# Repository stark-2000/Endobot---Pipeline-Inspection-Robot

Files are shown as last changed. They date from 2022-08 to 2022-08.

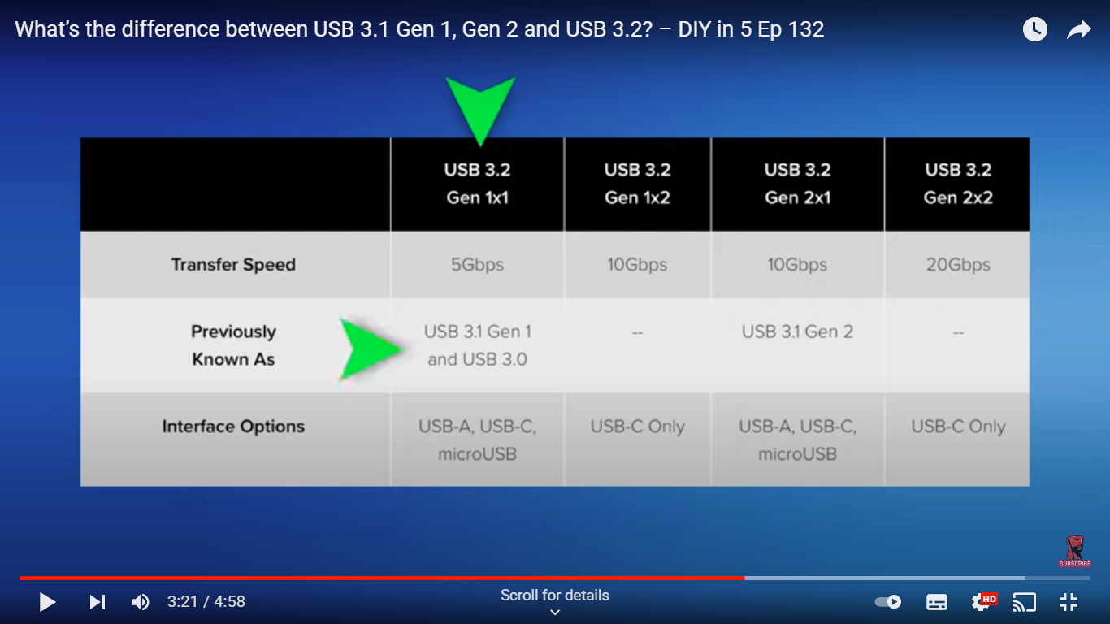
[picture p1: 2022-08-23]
Modules/Controller/USB - Case Study/USB Standards - Explained.png

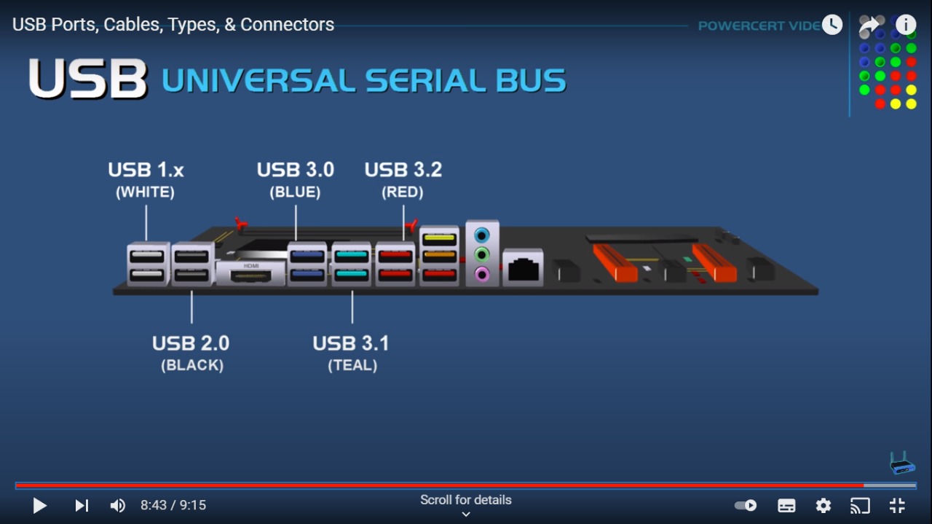
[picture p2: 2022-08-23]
Modules/Controller/USB - Case Study/USB Color Coding.jpeg

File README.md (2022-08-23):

Endobot 2.0, a tethered pipeline inspection robot which can detect leaks, corrosion and defects on pipelines as small as 4 inch up-to a depth of 300 meters and can withstand 5 bar underwater pressure.
It uses RS422 long distance data transfer protocol for camera feed & data transfer. The robot can be fully controlled from outside the pipeline using sophisticated controllers which enable 4 wheel drive and advanced transmission. 
Onboard IMU & Encoders enable accurate localisation & distance calculation of the robot. Realtime motor temp, indoor temp, pipeline leak sounds, current consumption, inclination calculation is all performed and displayed on a mini LCD screen.

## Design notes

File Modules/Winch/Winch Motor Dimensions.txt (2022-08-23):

Straight shaft motor: 
Case 1: 12cm max body length [done] (mounting outside spool perpendicular to spool axis)
Case 2: 30cm max body length [done] (mounting inside spool)
Case 3: Small length more dia (fat BLDC motor) [not available]

90 degree motor - 12cm max [2 vendors, one is WP AC motor, other chinese guy]

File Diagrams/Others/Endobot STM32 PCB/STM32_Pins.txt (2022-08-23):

TIM 1, 2, 3, 4, 5, 8, 9, 12 (Timers with PWM)

SPI4_SCK - White - PE12 - PWM - FT
SPI4_MISO - Blue - PE13 - PWM - FT
SPI4_MOSI - Green - PE14 - PWM - FT
SPI4_CS2 - Orange - PB12 - PWM - FT
GPIO_PB9 - Yellow - PB9 - PWM - FT
GPIO_PA10 - Brown - PA10 - PWM - FT

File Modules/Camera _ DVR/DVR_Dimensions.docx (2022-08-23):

DVR Layout

71mmm

51mm

Connectors

Record Stop

Joy Stick

Power ON/OFF

Logo

Distance Meter

LCD Screen

Screen Protection

- The DVR will have a battery backup of at least 1 Hour.

Depth - 50mm

110mm

190mm

Menu | Escape | Zoom in | Zoom Out

DVR Power ON/OFF Switch

Record Start

MIC (Push Button)

Screenshot

70mm

USB Storage Slot

Keyboard

90mm

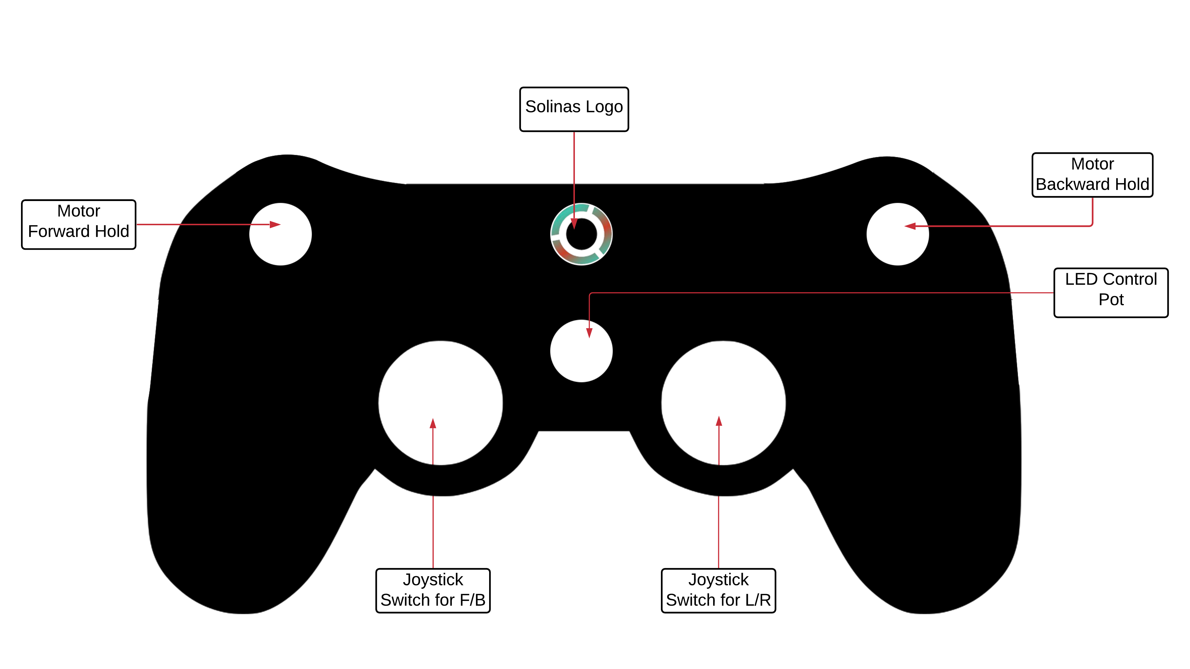
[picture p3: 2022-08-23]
Modules/Controller/Controller Design/Controller Design (labelled).png

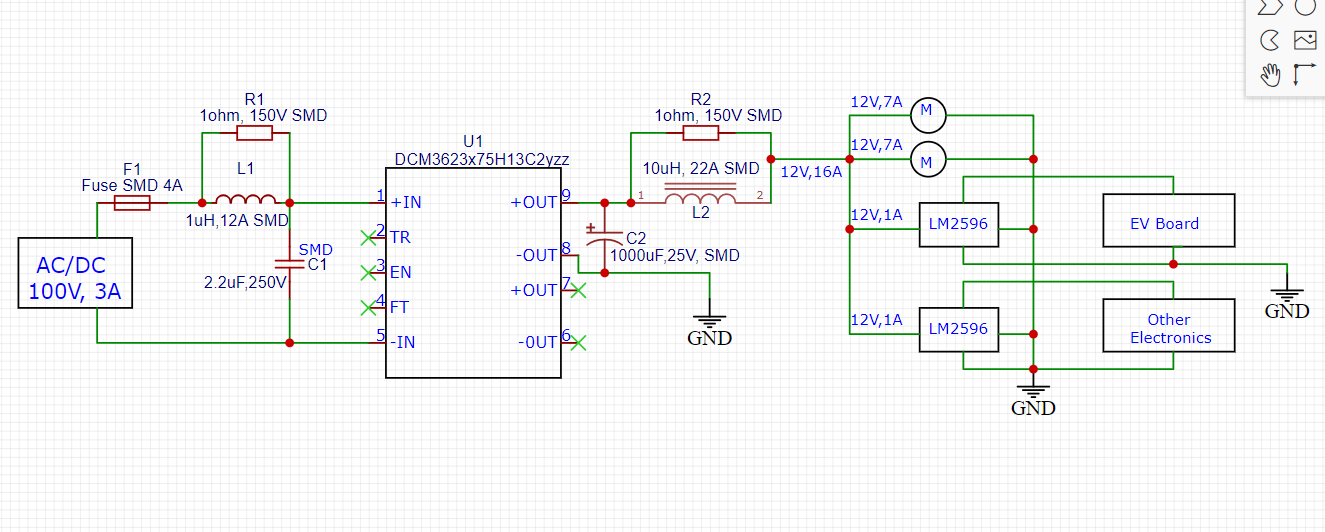
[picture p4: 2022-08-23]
Modules/Power Electronics/DC-DC Buck Converter/Vicor DCM/Buck Application Circuit.PNG

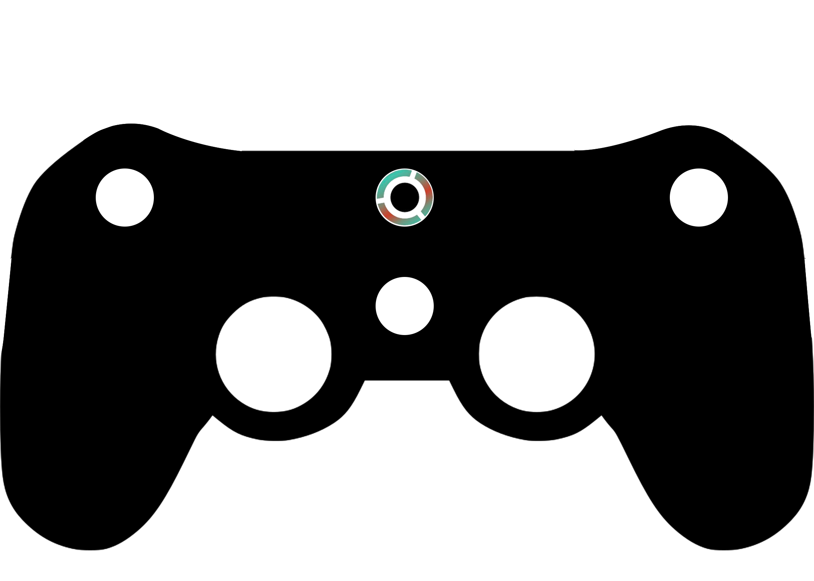
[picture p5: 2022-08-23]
Modules/Controller/Controller Design/Controller Design.png

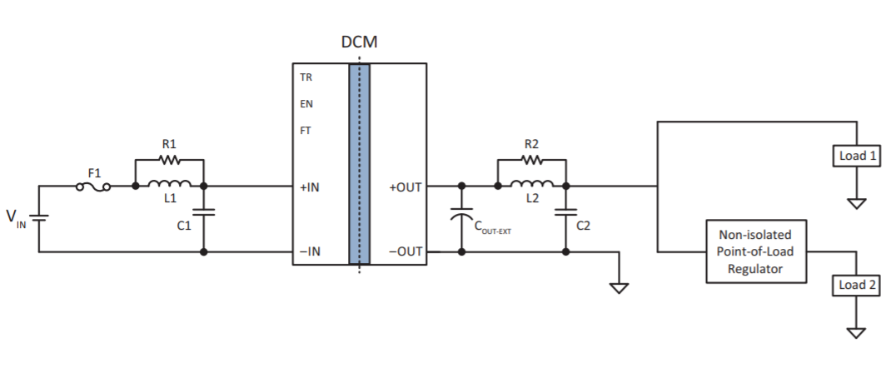
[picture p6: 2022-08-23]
Modules/Power Electronics/DC-DC Buck Converter/Vicor DCM/Buck 1 (DCM).PNG

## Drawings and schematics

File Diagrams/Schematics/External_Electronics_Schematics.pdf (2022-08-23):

## DC - DC Buck 24V

## SMPS 120V 5A DC

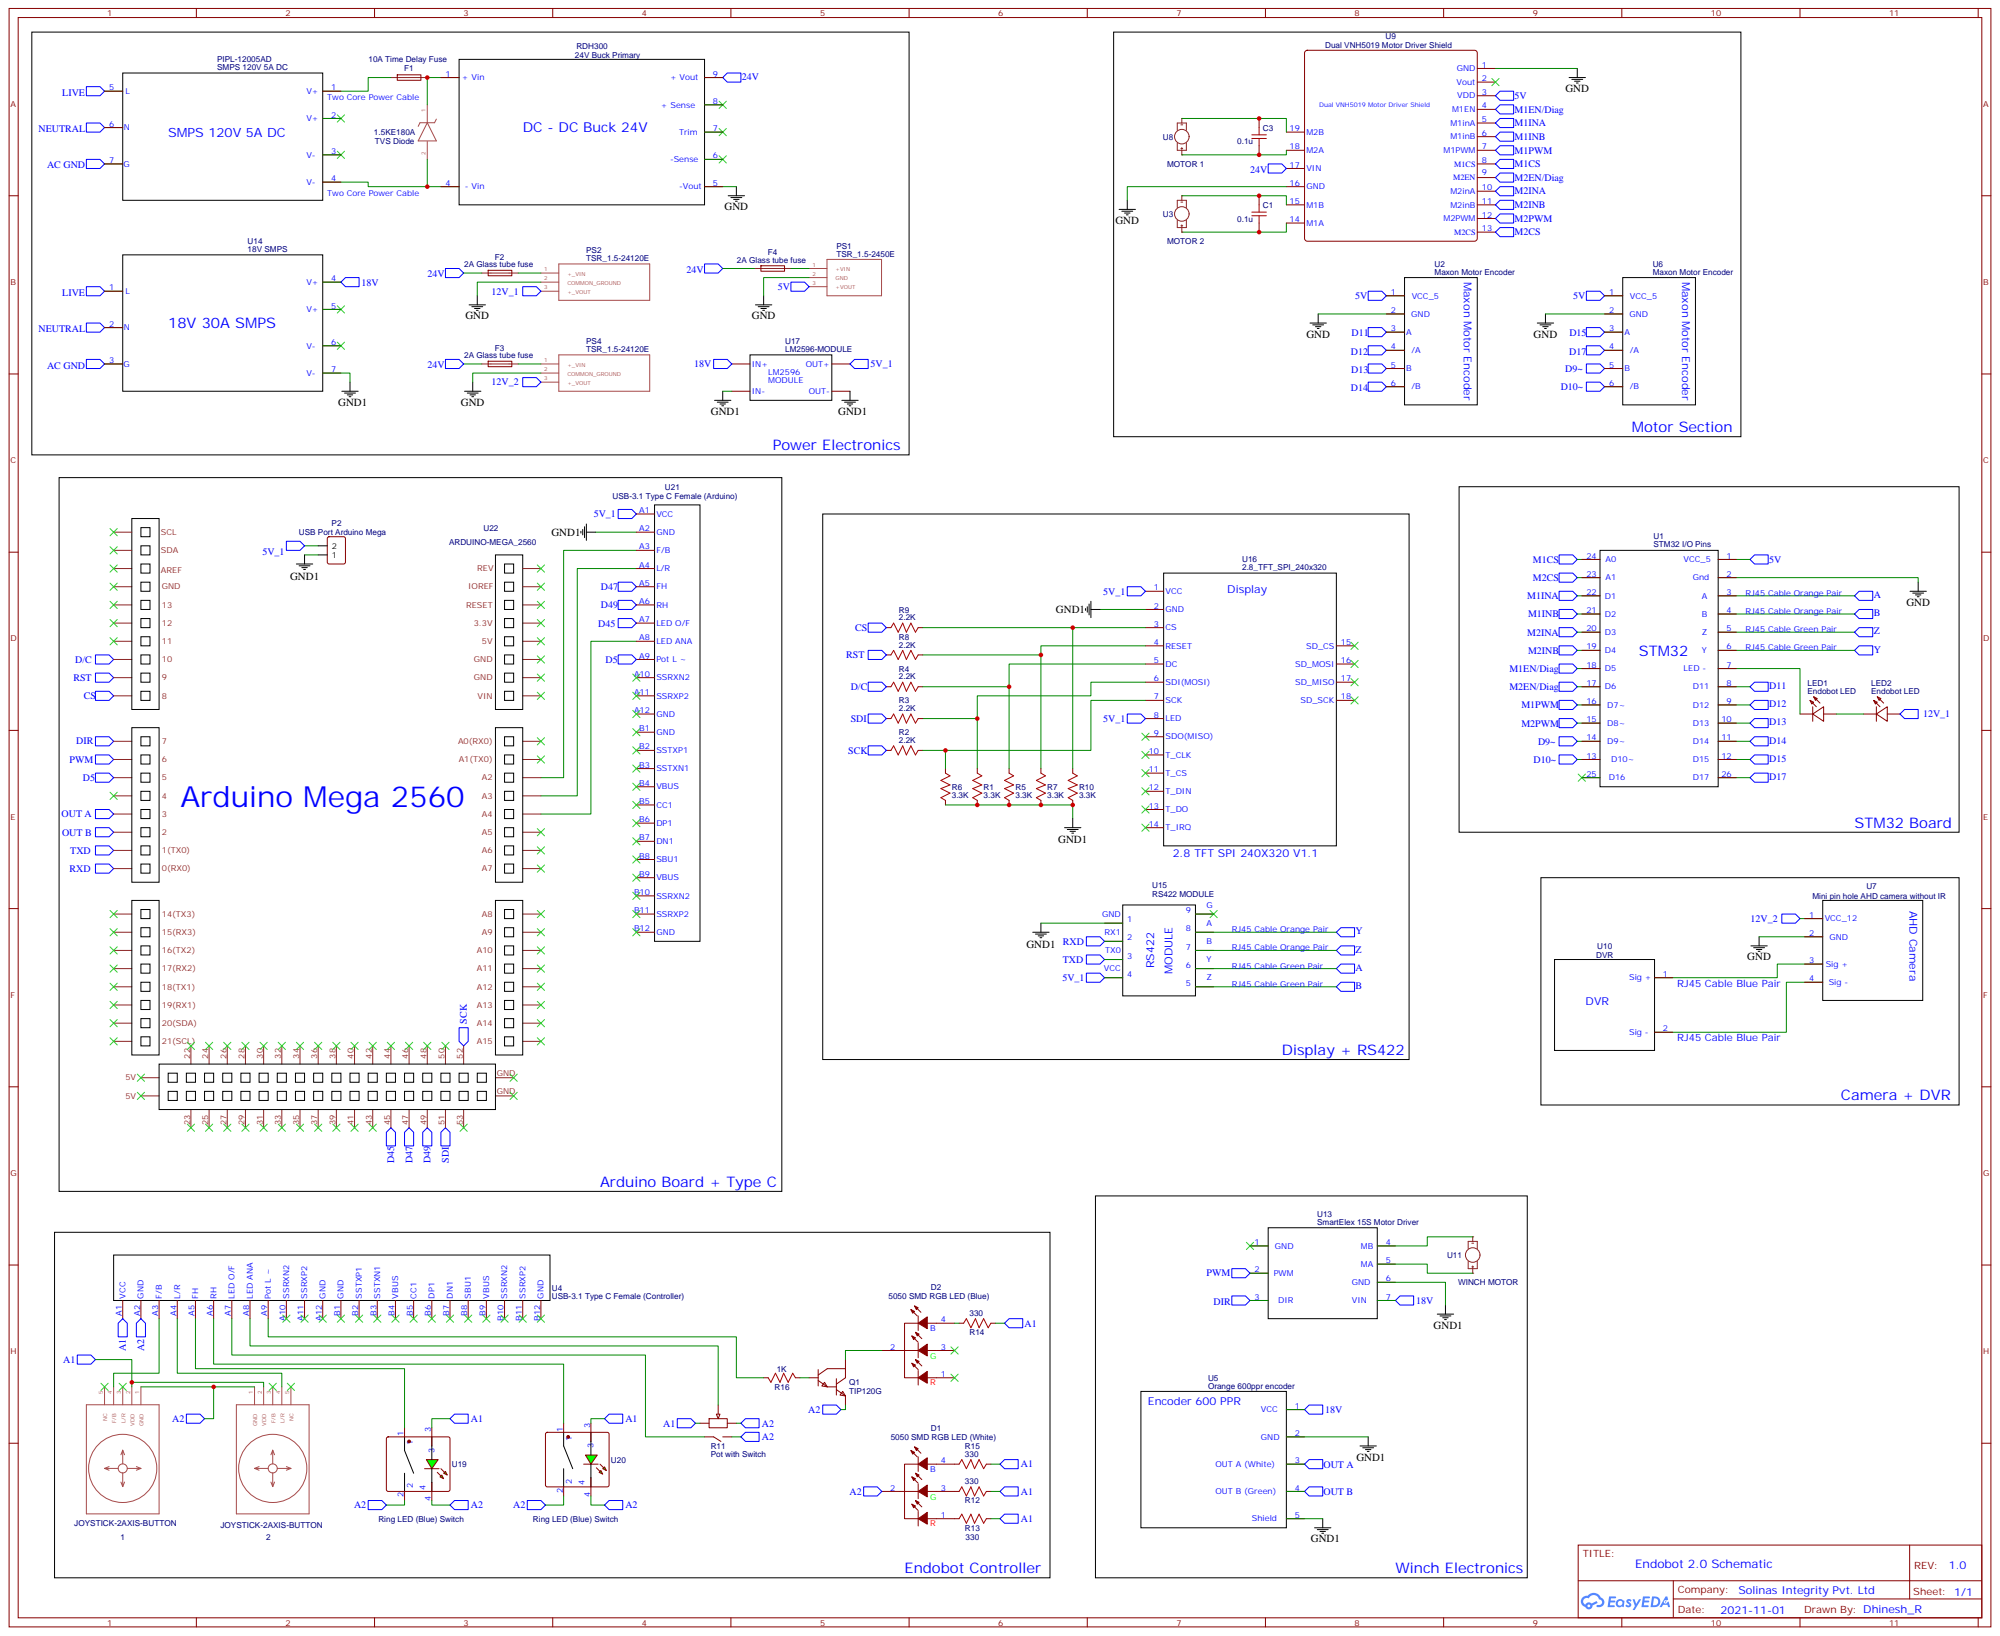
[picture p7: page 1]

Dual VNH5019 Motor Driver Shield

Two Core Power Cable

USB Port Arduino Mega

5050 SMD RGB LED (Blue)

Ring LED (Blue) Switch

Company: Solinas Integrity Pvt. Ltd

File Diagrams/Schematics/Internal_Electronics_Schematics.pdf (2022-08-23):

## Microcontroller Essentials

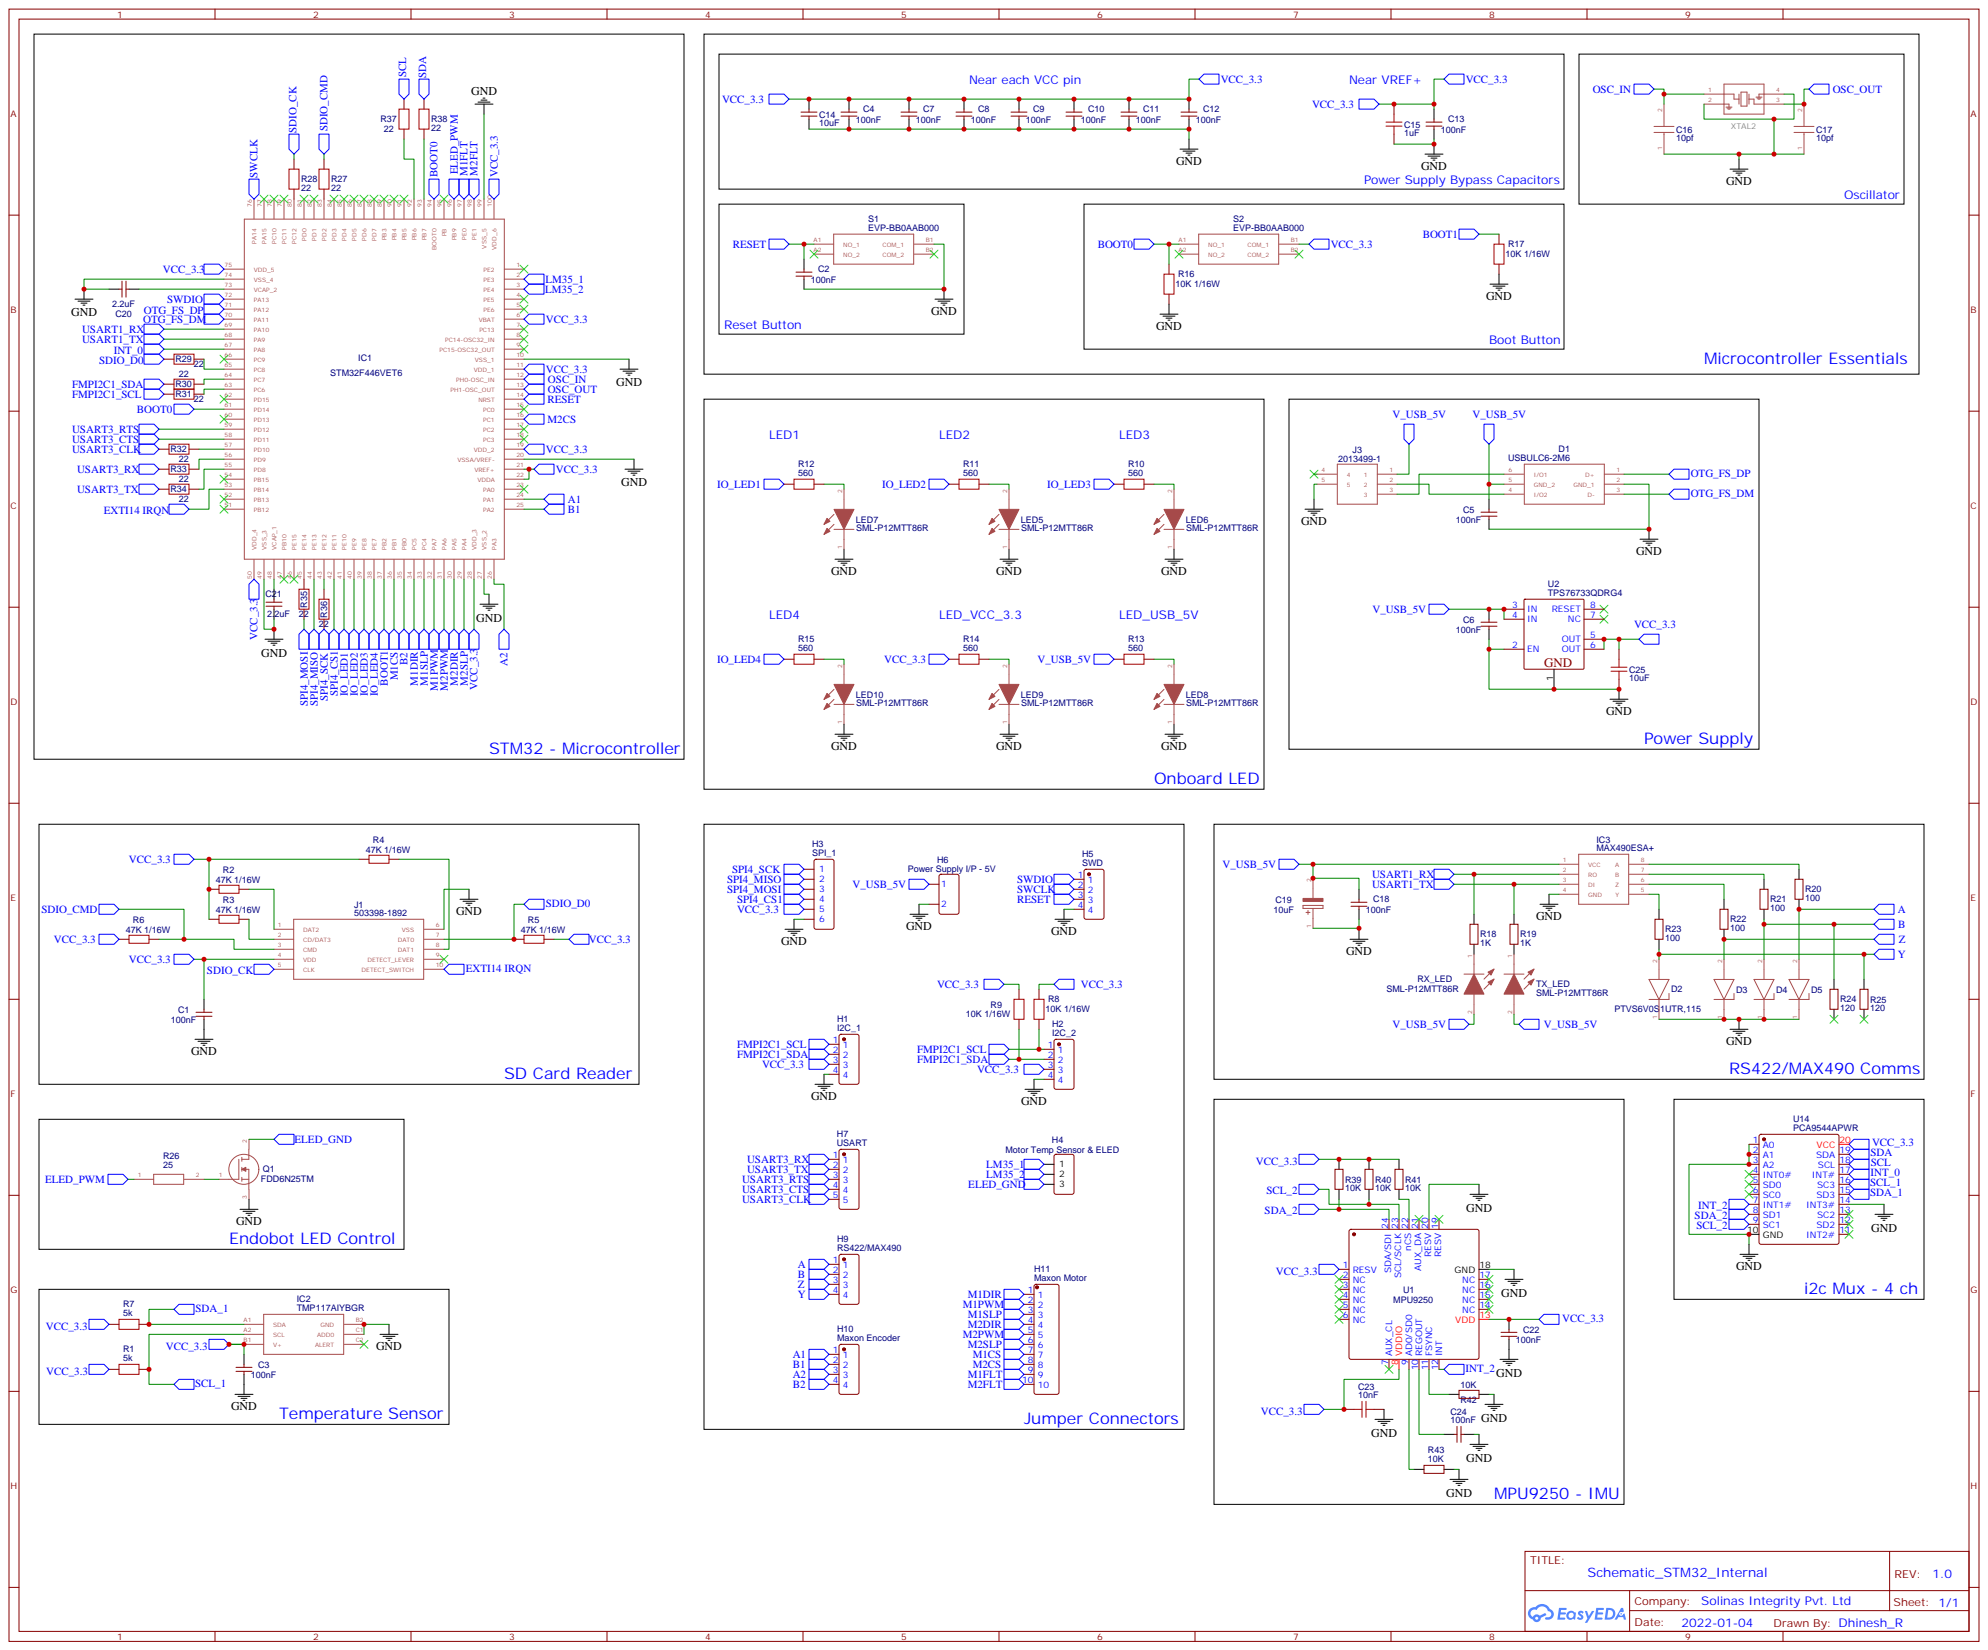
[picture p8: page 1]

Power Supply Bypass Capacitors

Company: Solinas Integrity Pvt. Ltd

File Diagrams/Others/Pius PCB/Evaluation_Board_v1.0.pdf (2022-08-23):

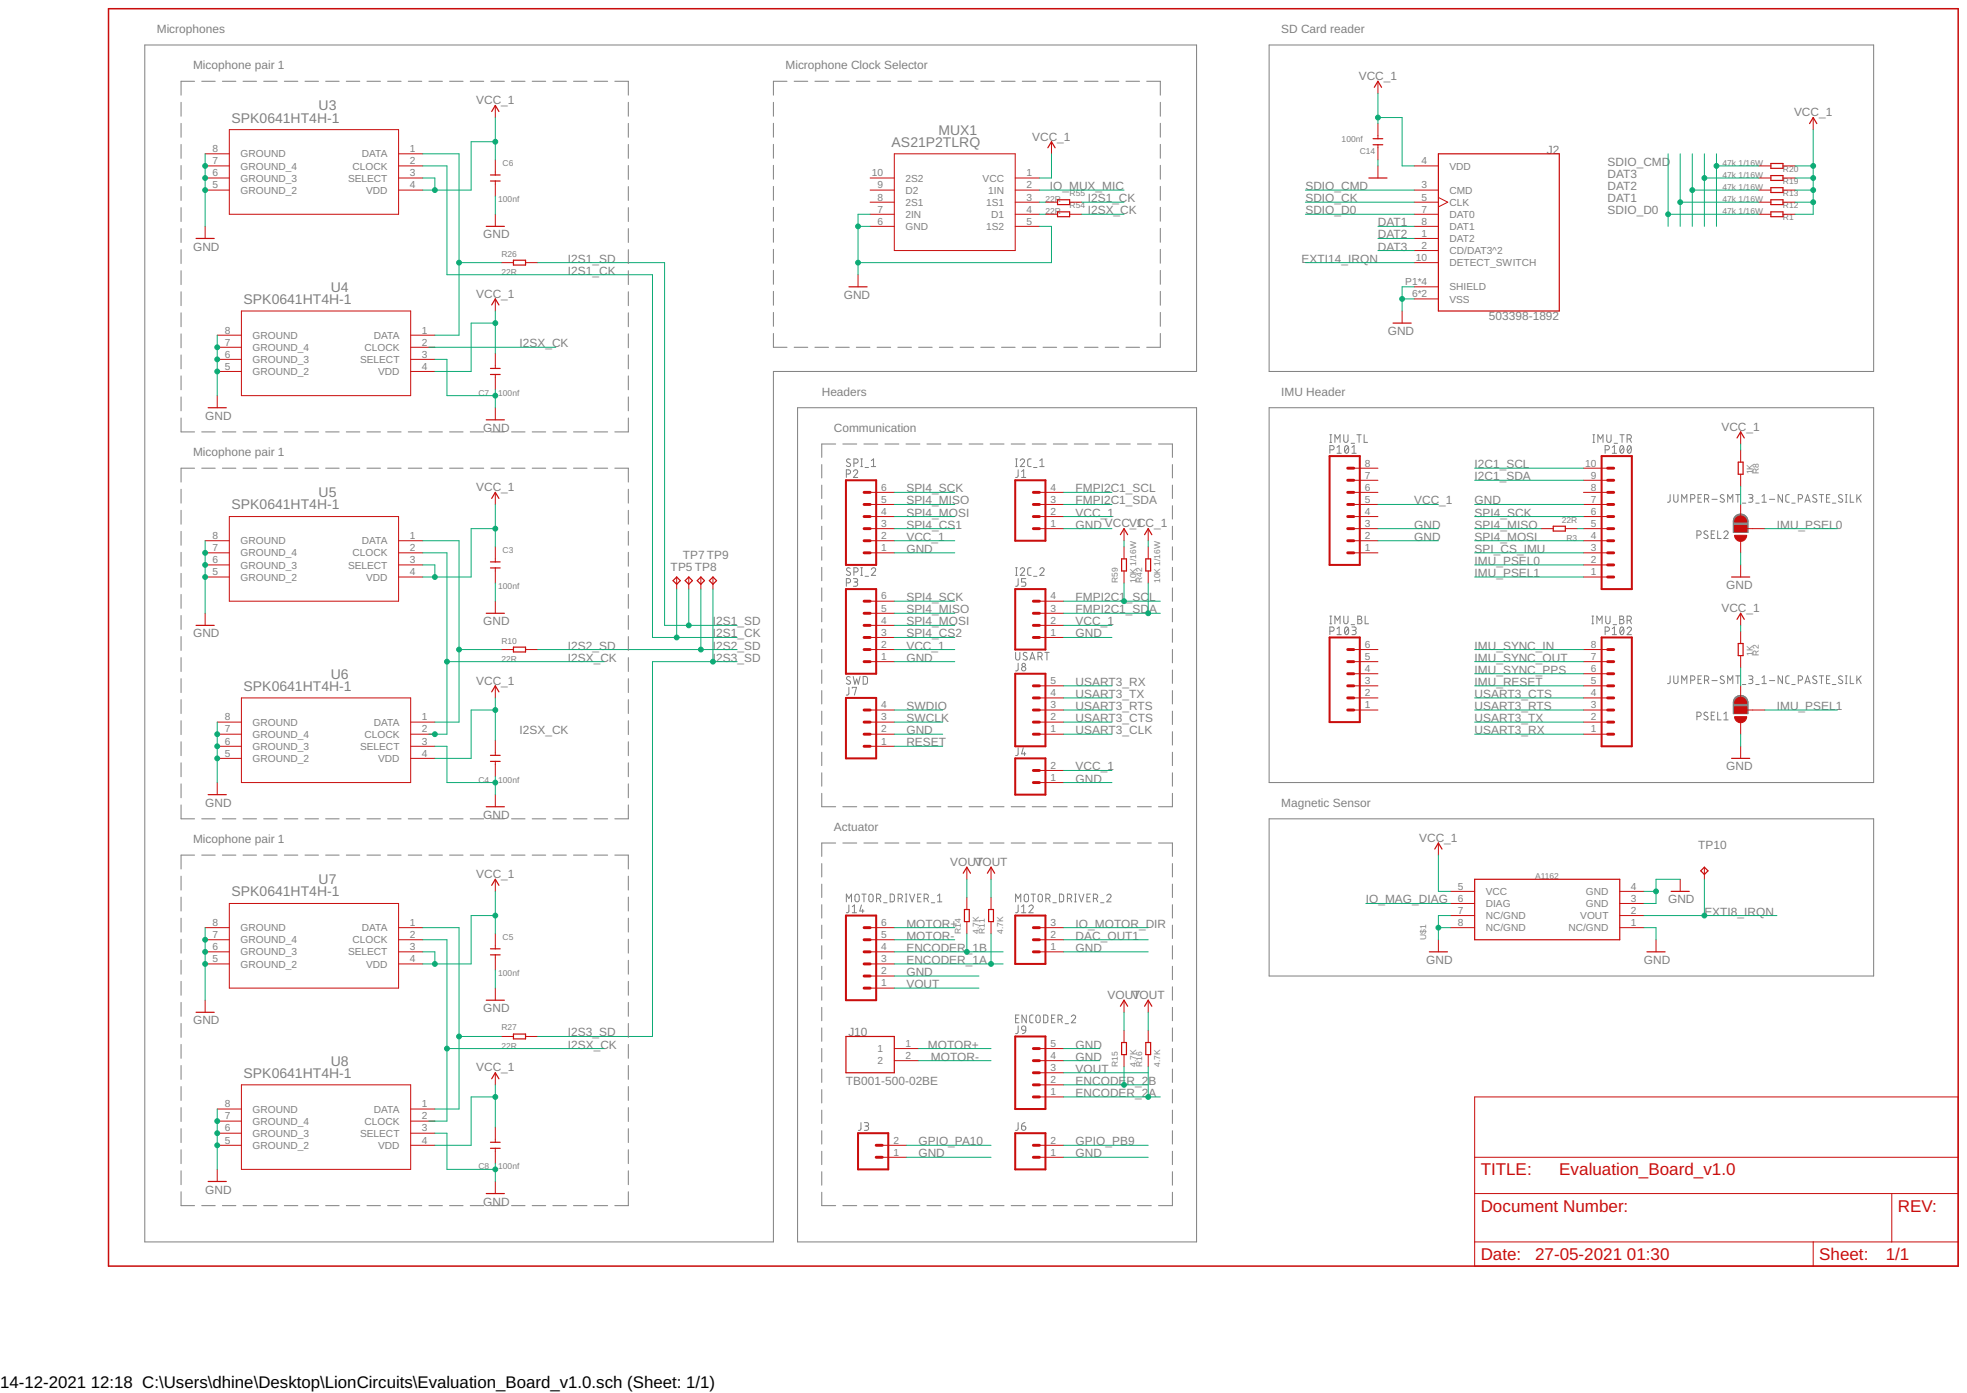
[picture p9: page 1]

Document Number: | REV:

Date: 27-05-2021 01:30 | Sheet: 1/1

14-12-2021 12:18 C:\Users\dhine\Desktop\LionCircuits\Evaluation_Board_v1.0.sch (Sheet: 1/1)

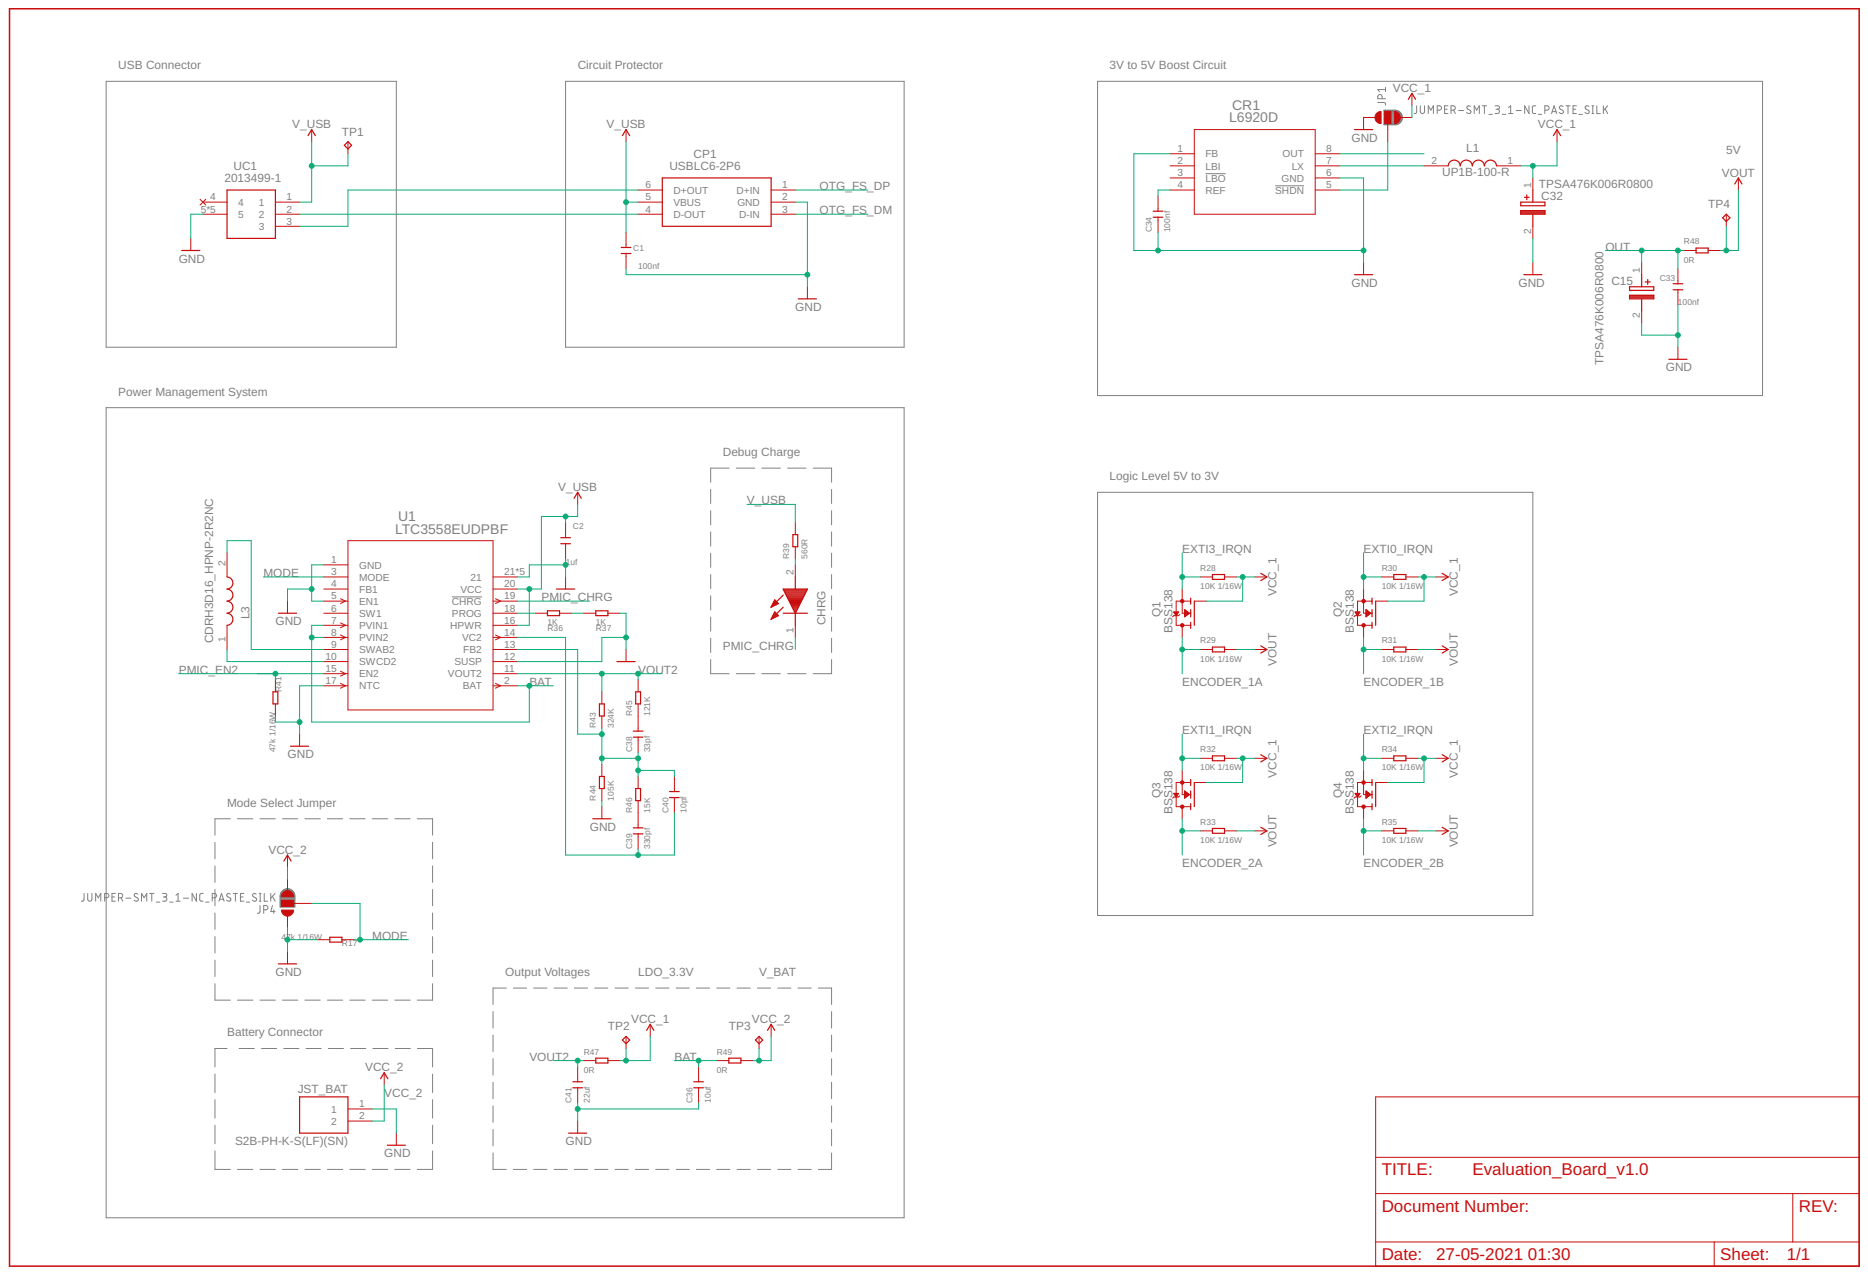
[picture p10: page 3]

Document Number: | REV:

Date: 27-05-2021 01:30 | Sheet: 1/1

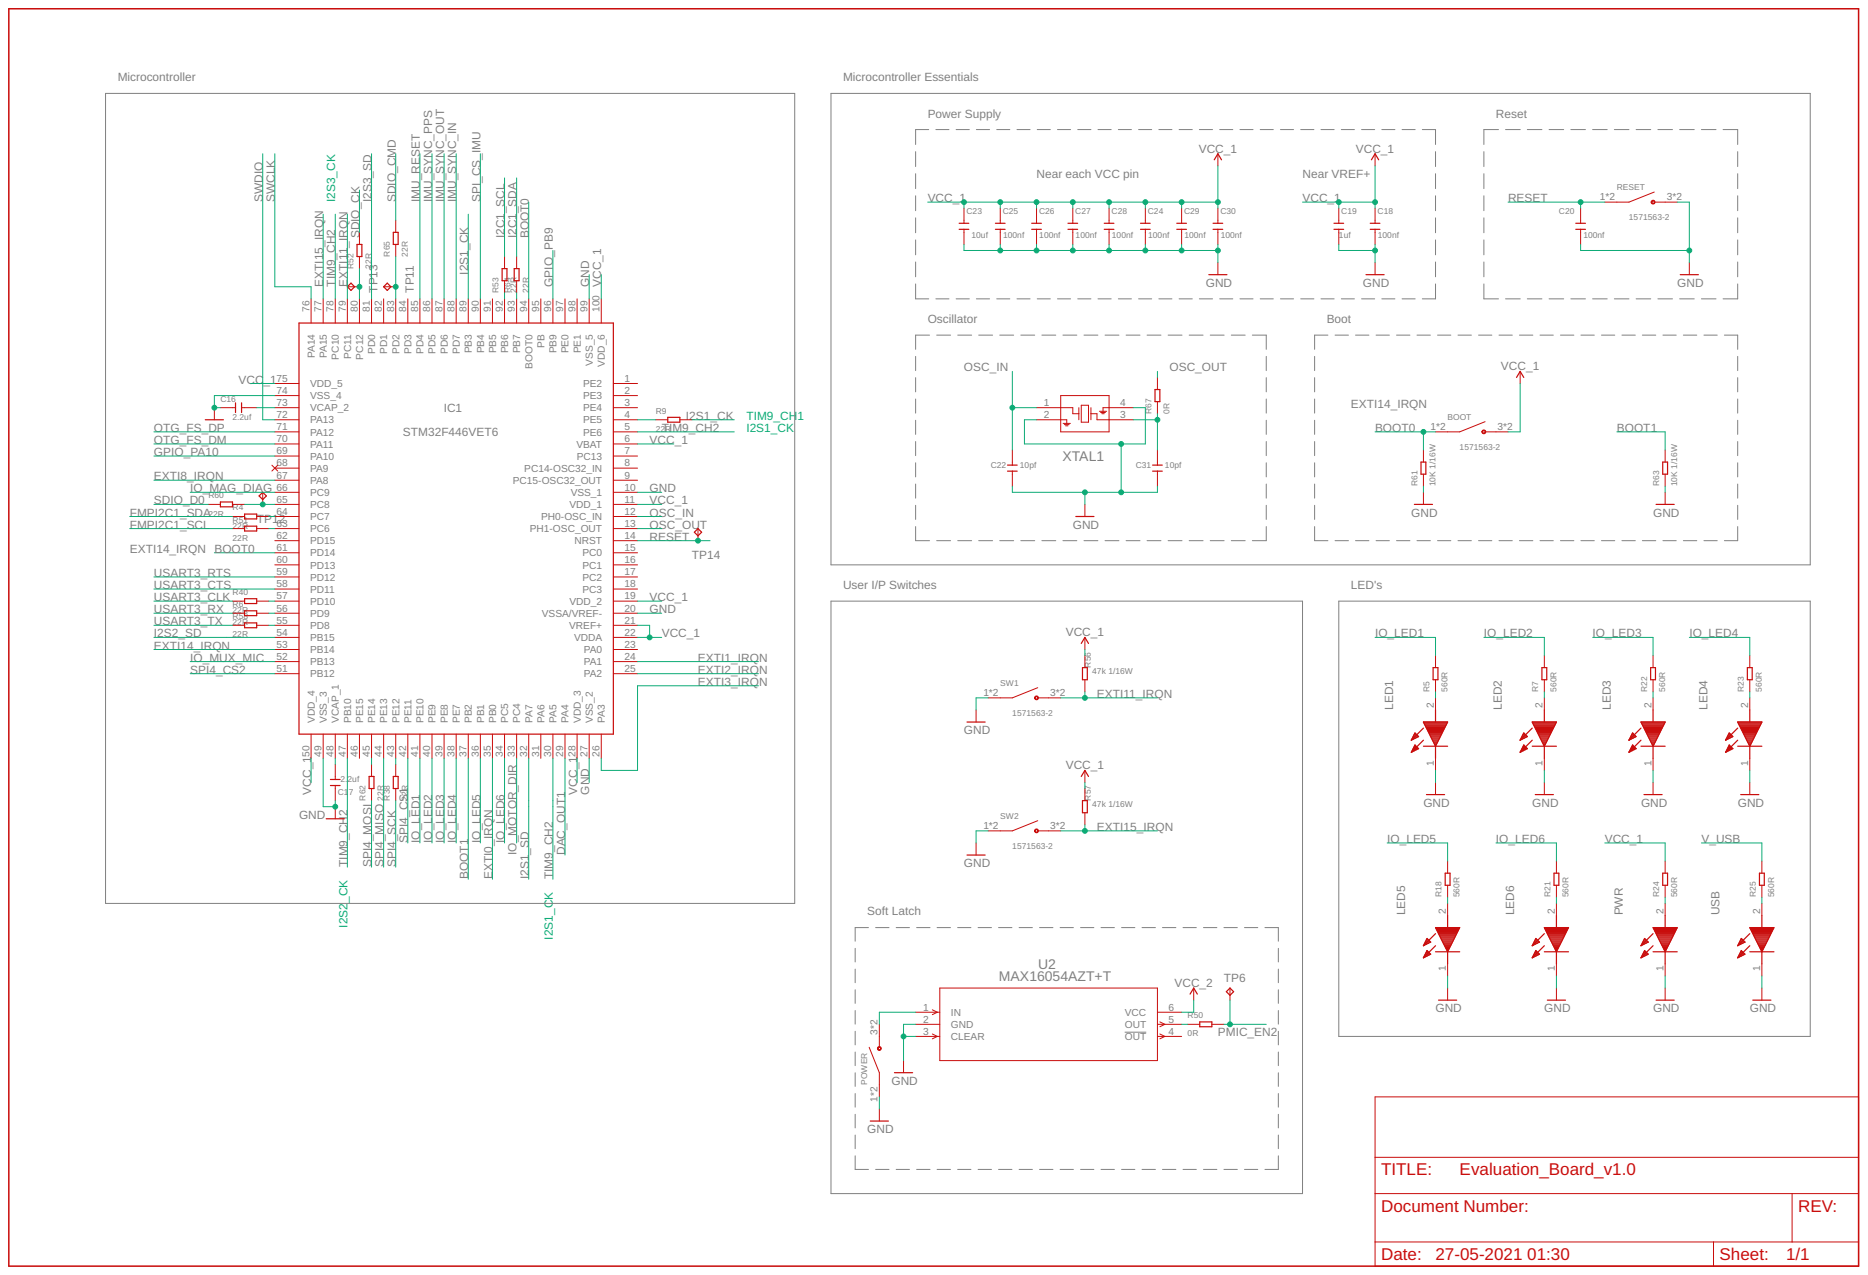
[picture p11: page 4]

Document Number: | REV:

Date: 27-05-2021 01:30 | Sheet: 1/1

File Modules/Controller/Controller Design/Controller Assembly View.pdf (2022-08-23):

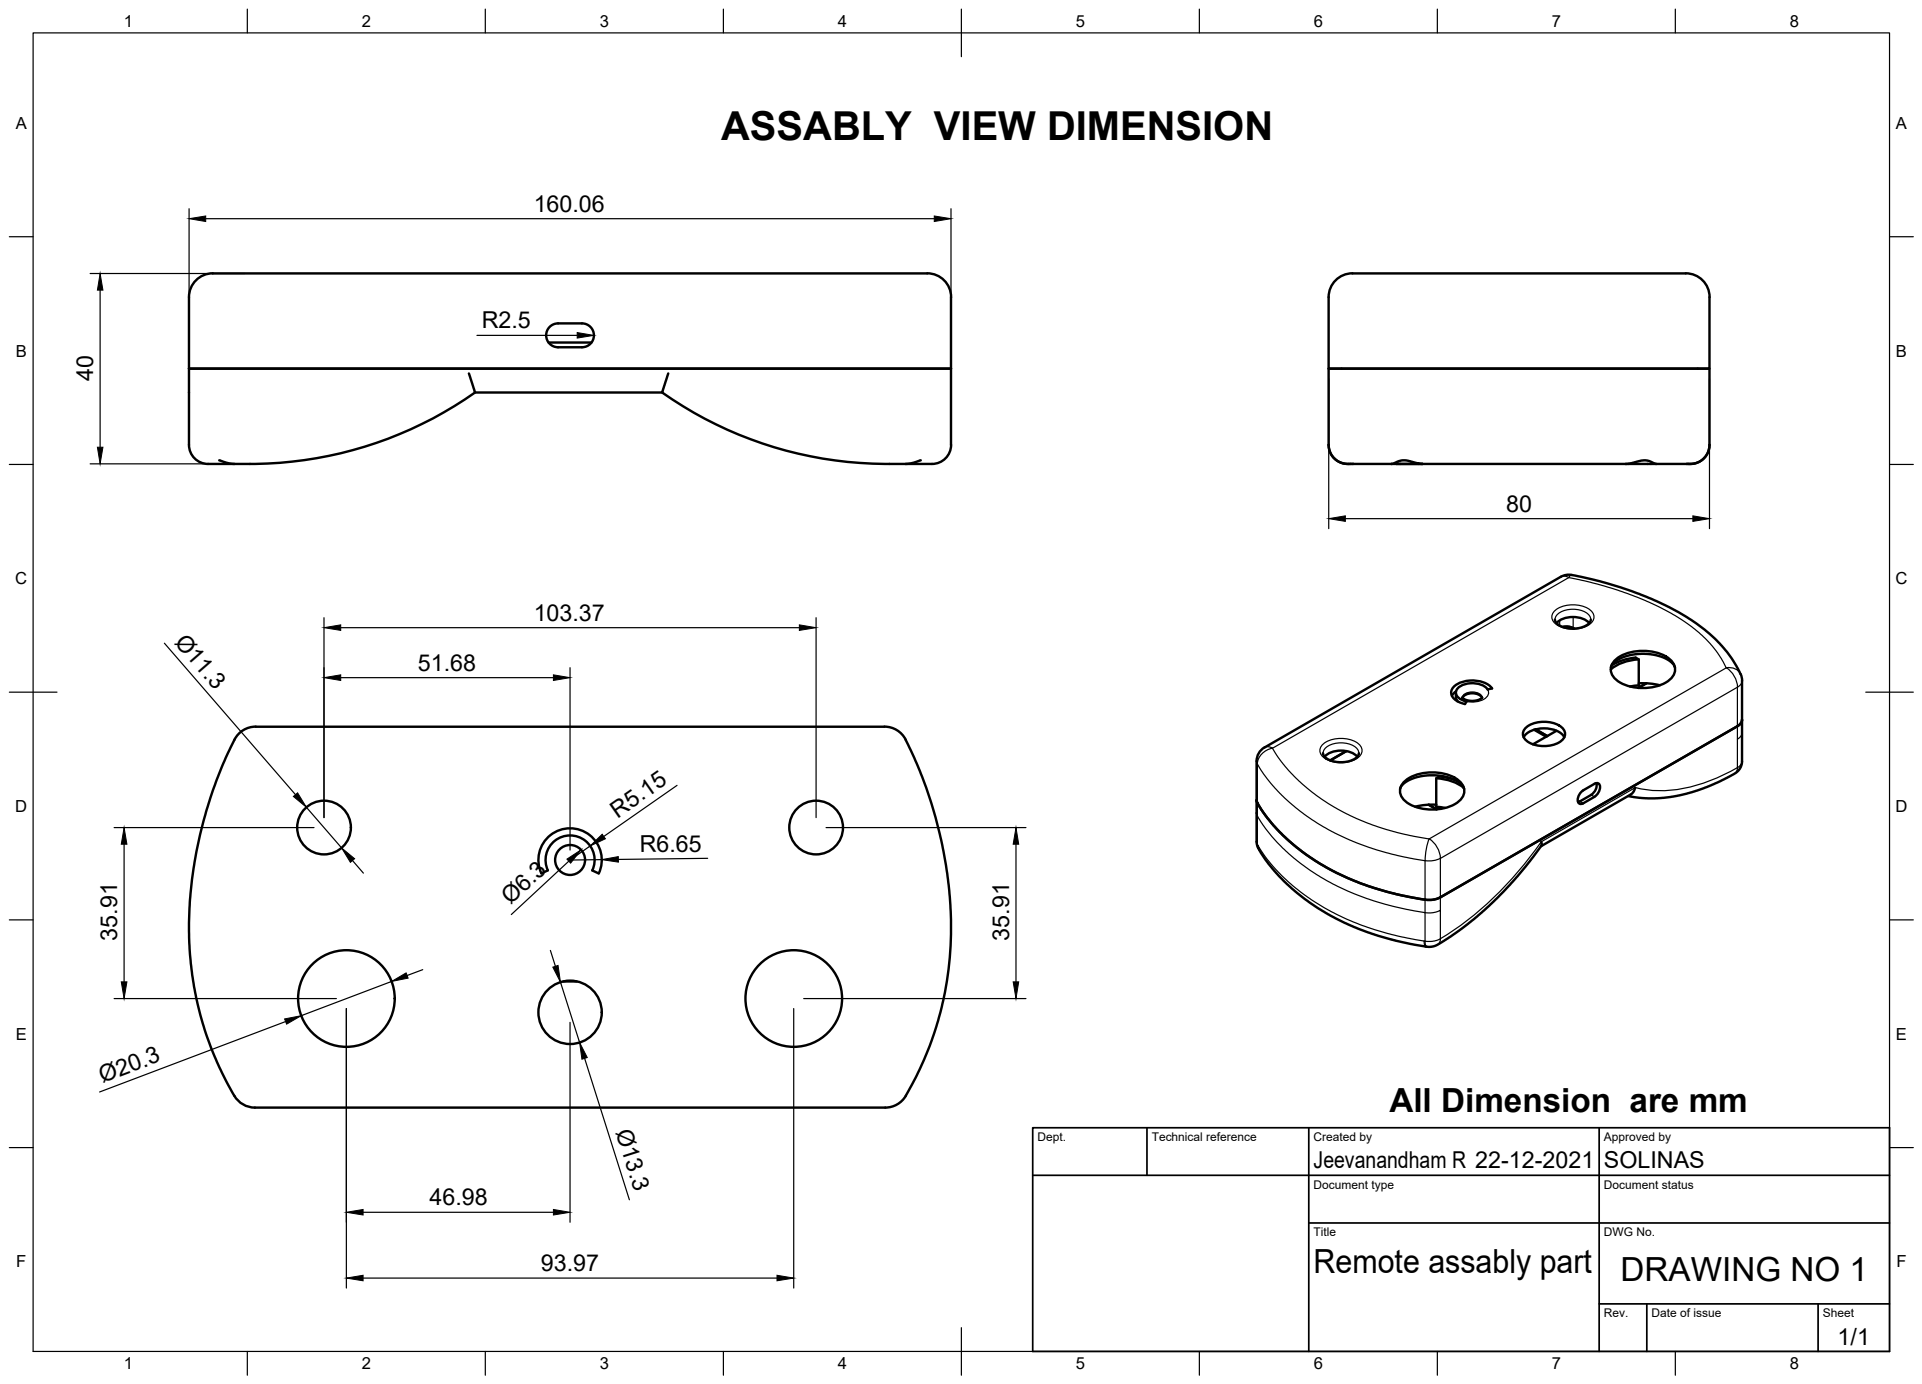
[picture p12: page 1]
Title; DWG No.; Rev.; Date of issue; Sheet; Remote assably part; DRAWING NO 1; Jeevanandham R; SOLINAS 40

ASSABLY VIEW DIMENSION

All Dimension are mm

Dept. | Technical reference | Created by 22-12-2021 | Approved by

Document type | Document status

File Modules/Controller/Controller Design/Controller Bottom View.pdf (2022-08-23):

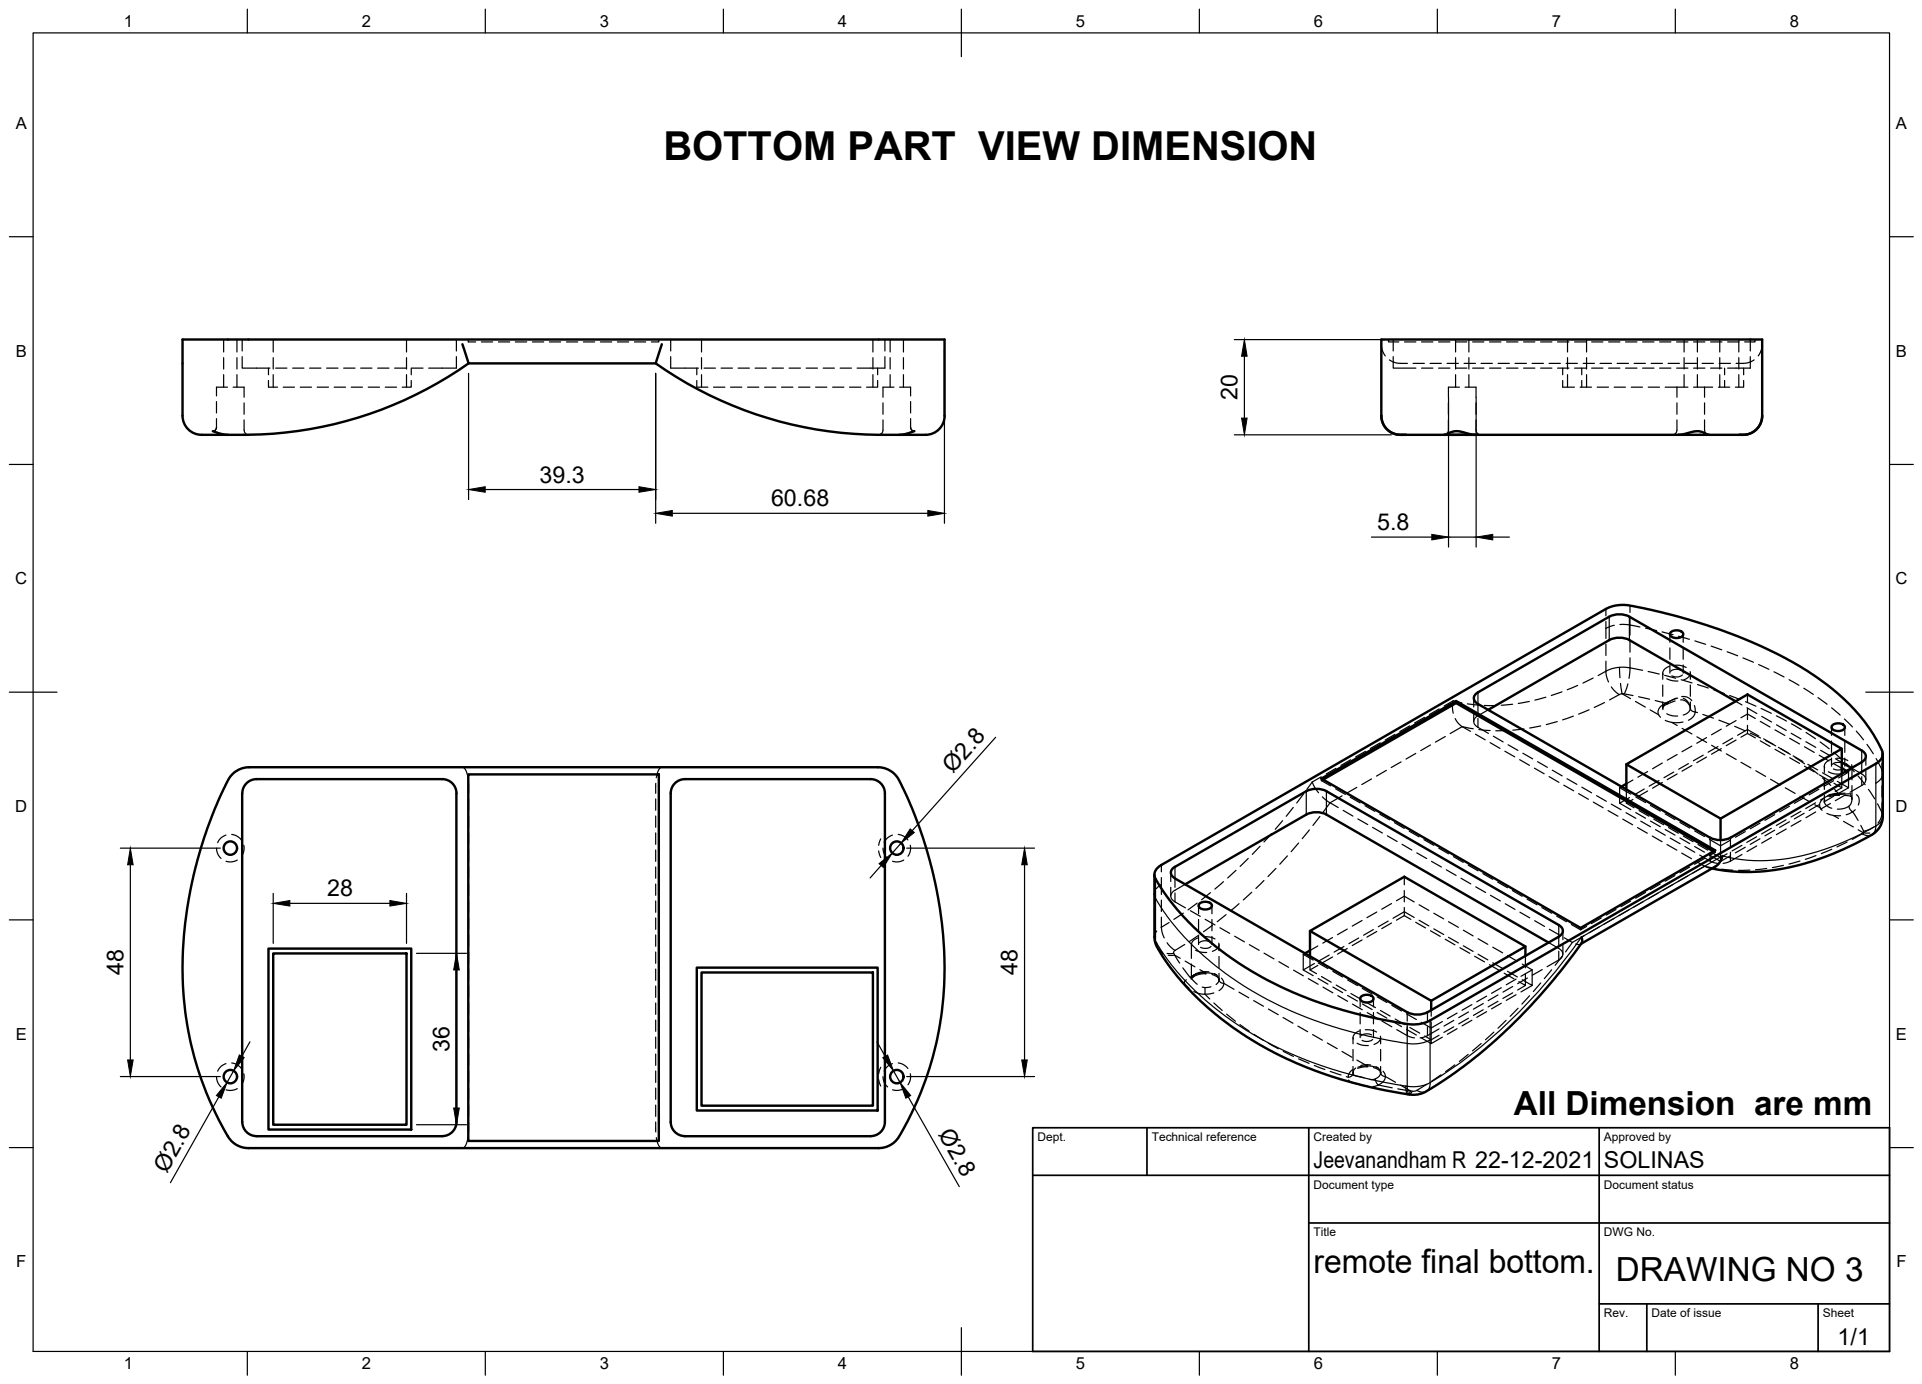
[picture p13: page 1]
Title; DWG No.; Rev.; Date of issue; Sheet

BOTTOM PART VIEW DIMENSION

All Dimension are mm

Dept. | Technical reference | Created by Jeevanandham R 22-12-2021 | Approved by SOLINAS

Document type | Document status

DRAWING NO 3 remote final bottom.

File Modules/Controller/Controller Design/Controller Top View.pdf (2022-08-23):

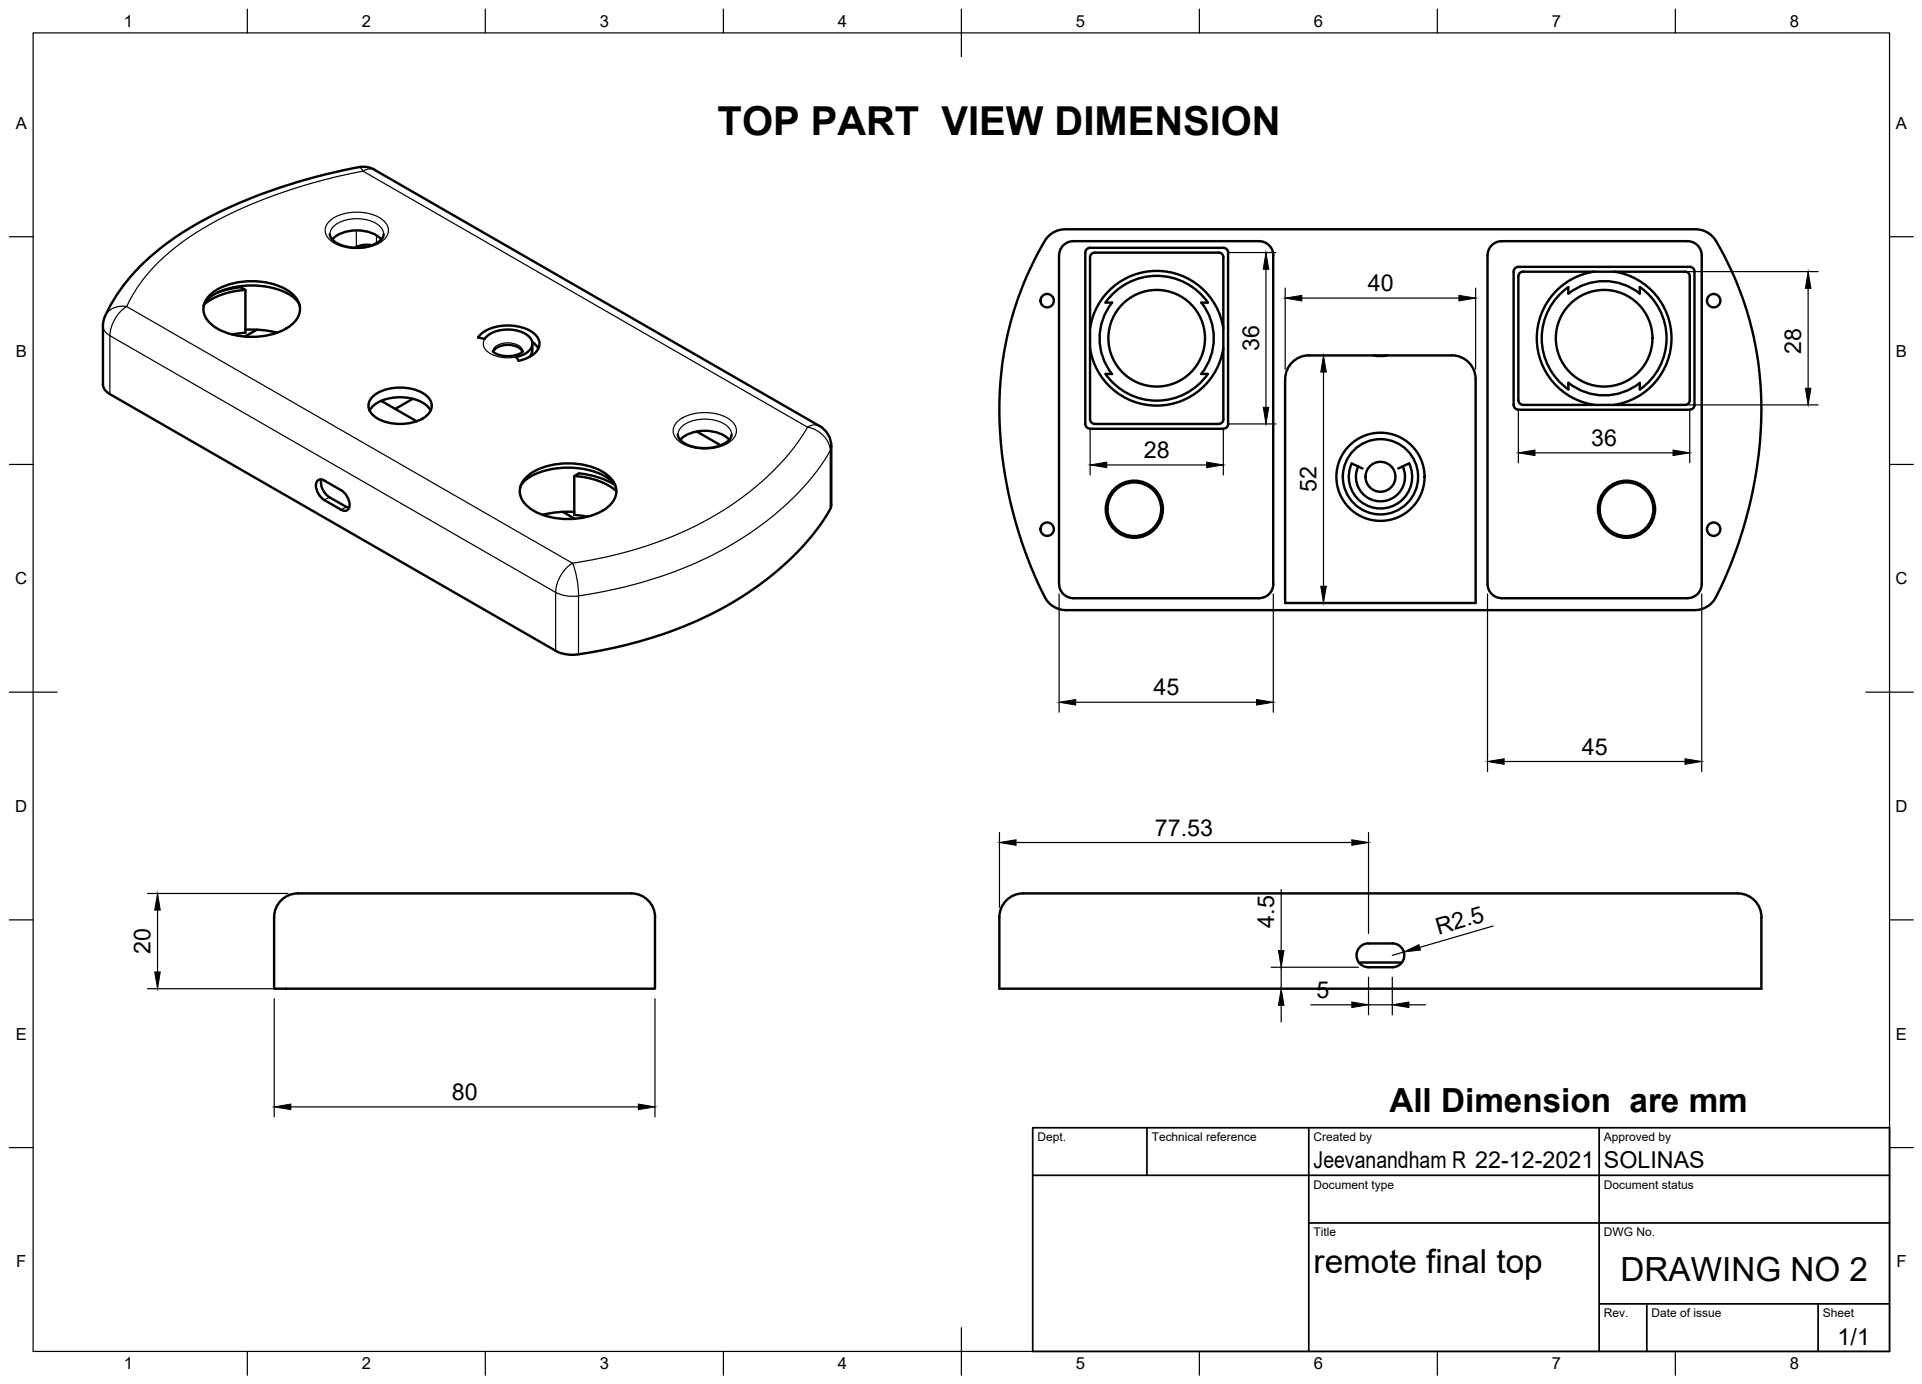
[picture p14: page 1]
Title; DWG No.; Rev.; Date of issue; Sheet; remote final top; DRAWING NO 2

TOP PART VIEW DIMENSION

All Dimension are mm

Dept. | Technical reference | Created by Jeevanandham R 22-12-2021 | Approved by SOLINAS

Document type | Document status

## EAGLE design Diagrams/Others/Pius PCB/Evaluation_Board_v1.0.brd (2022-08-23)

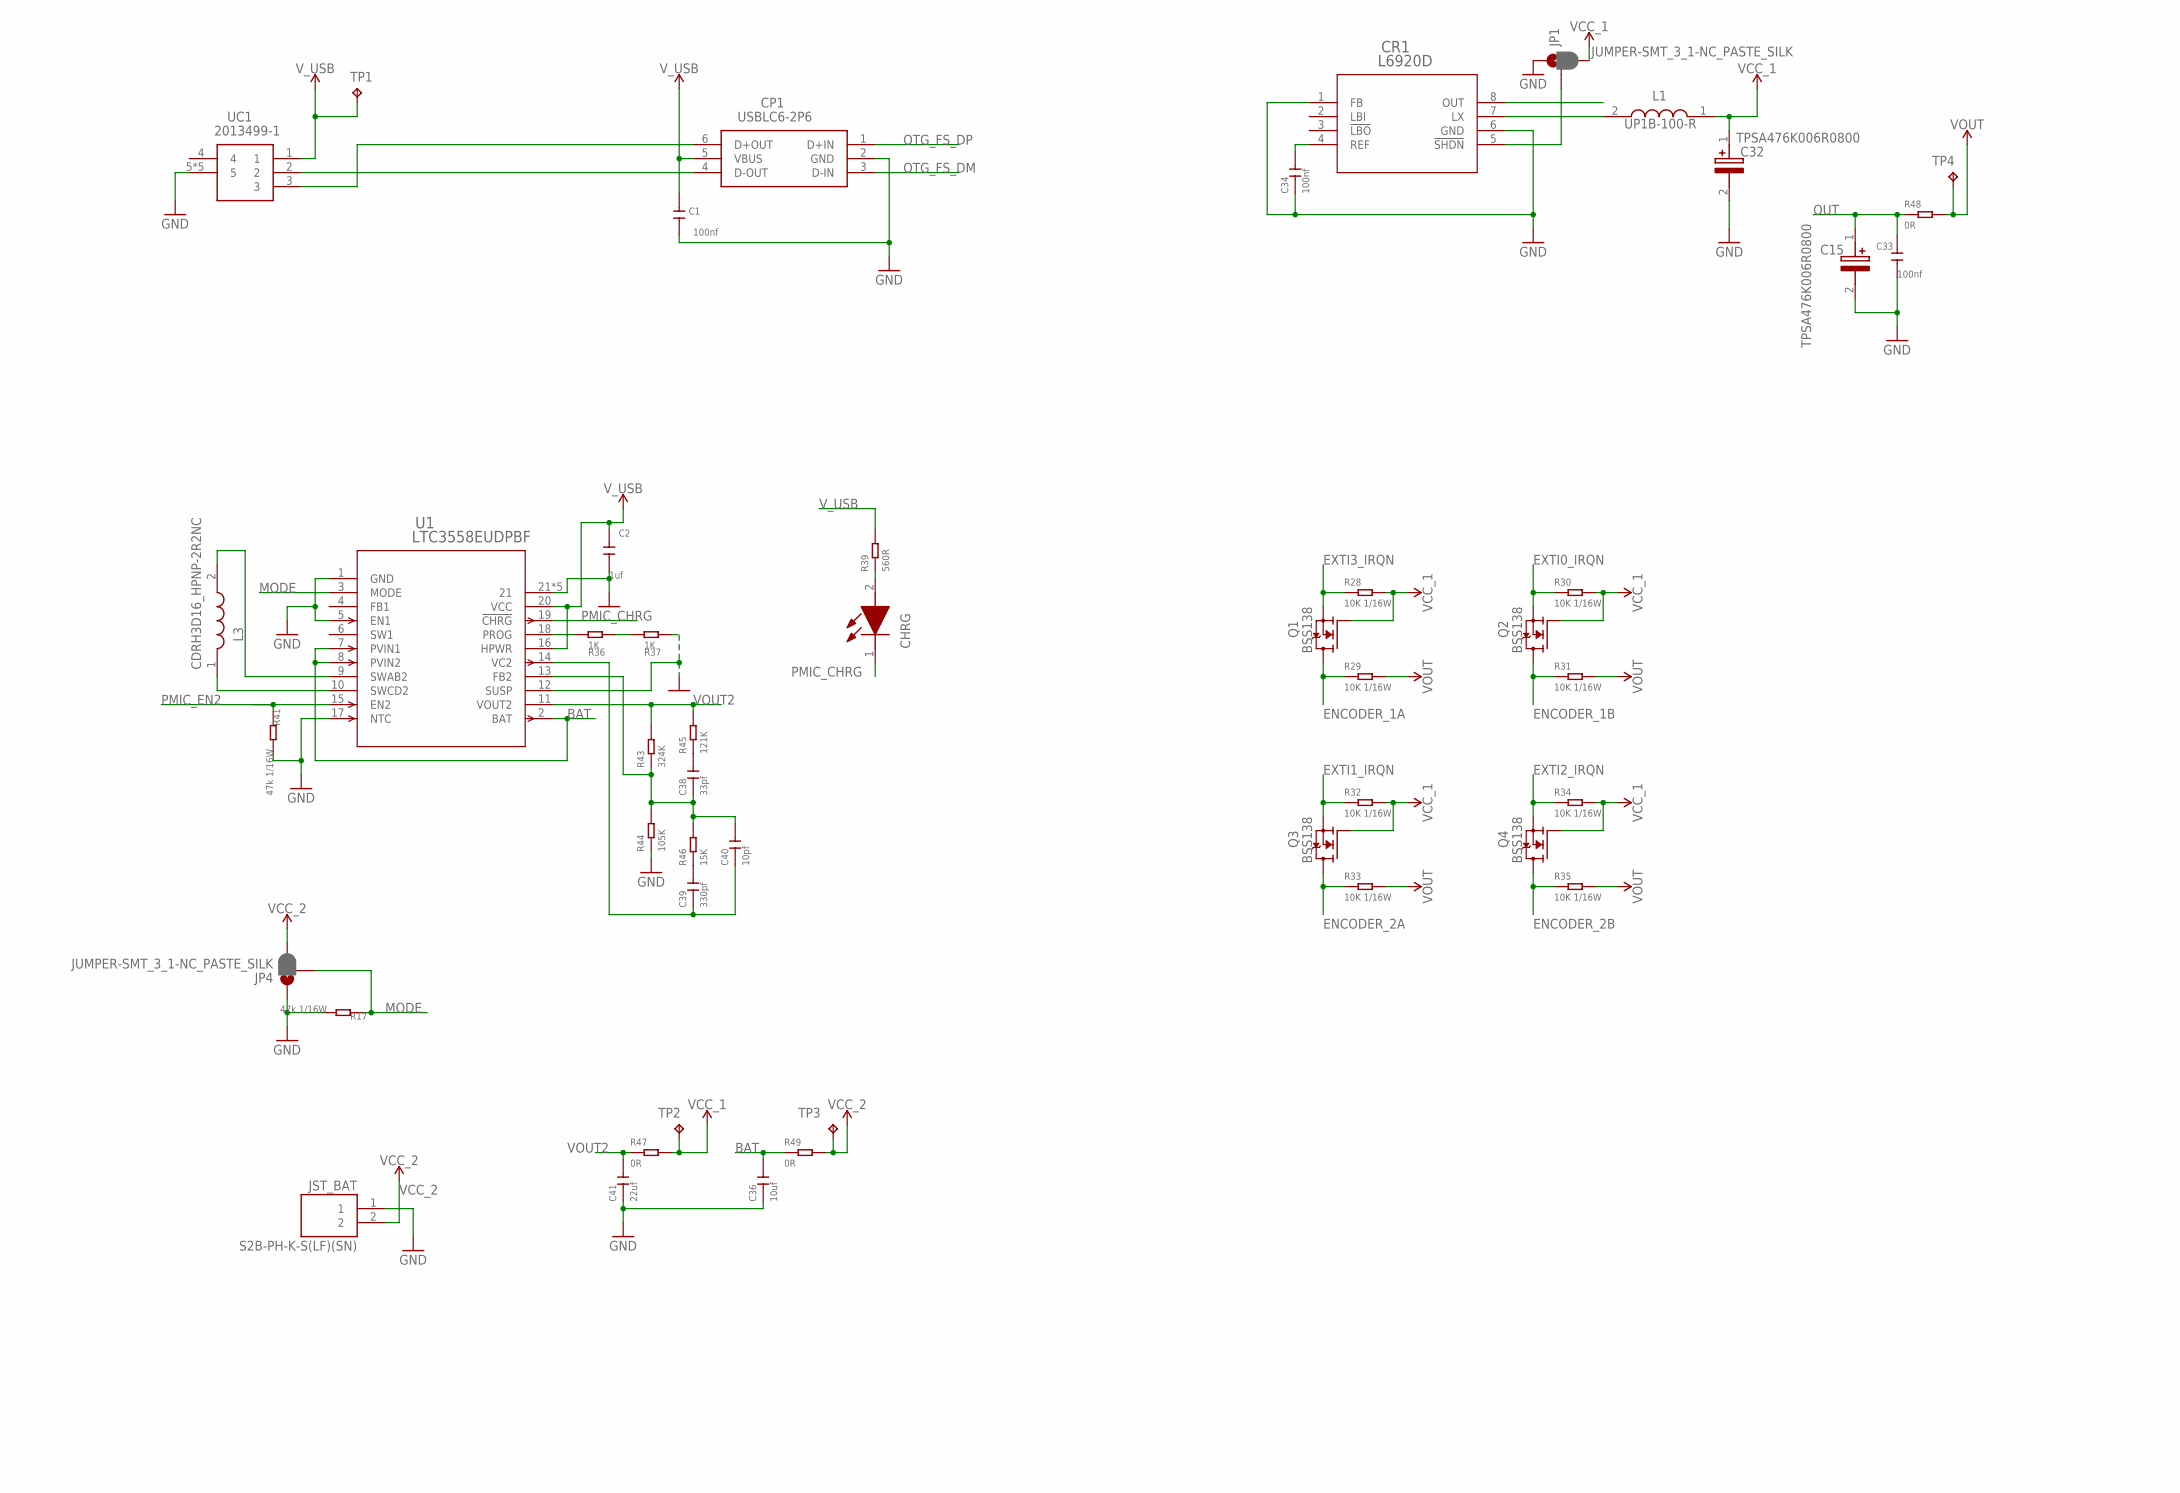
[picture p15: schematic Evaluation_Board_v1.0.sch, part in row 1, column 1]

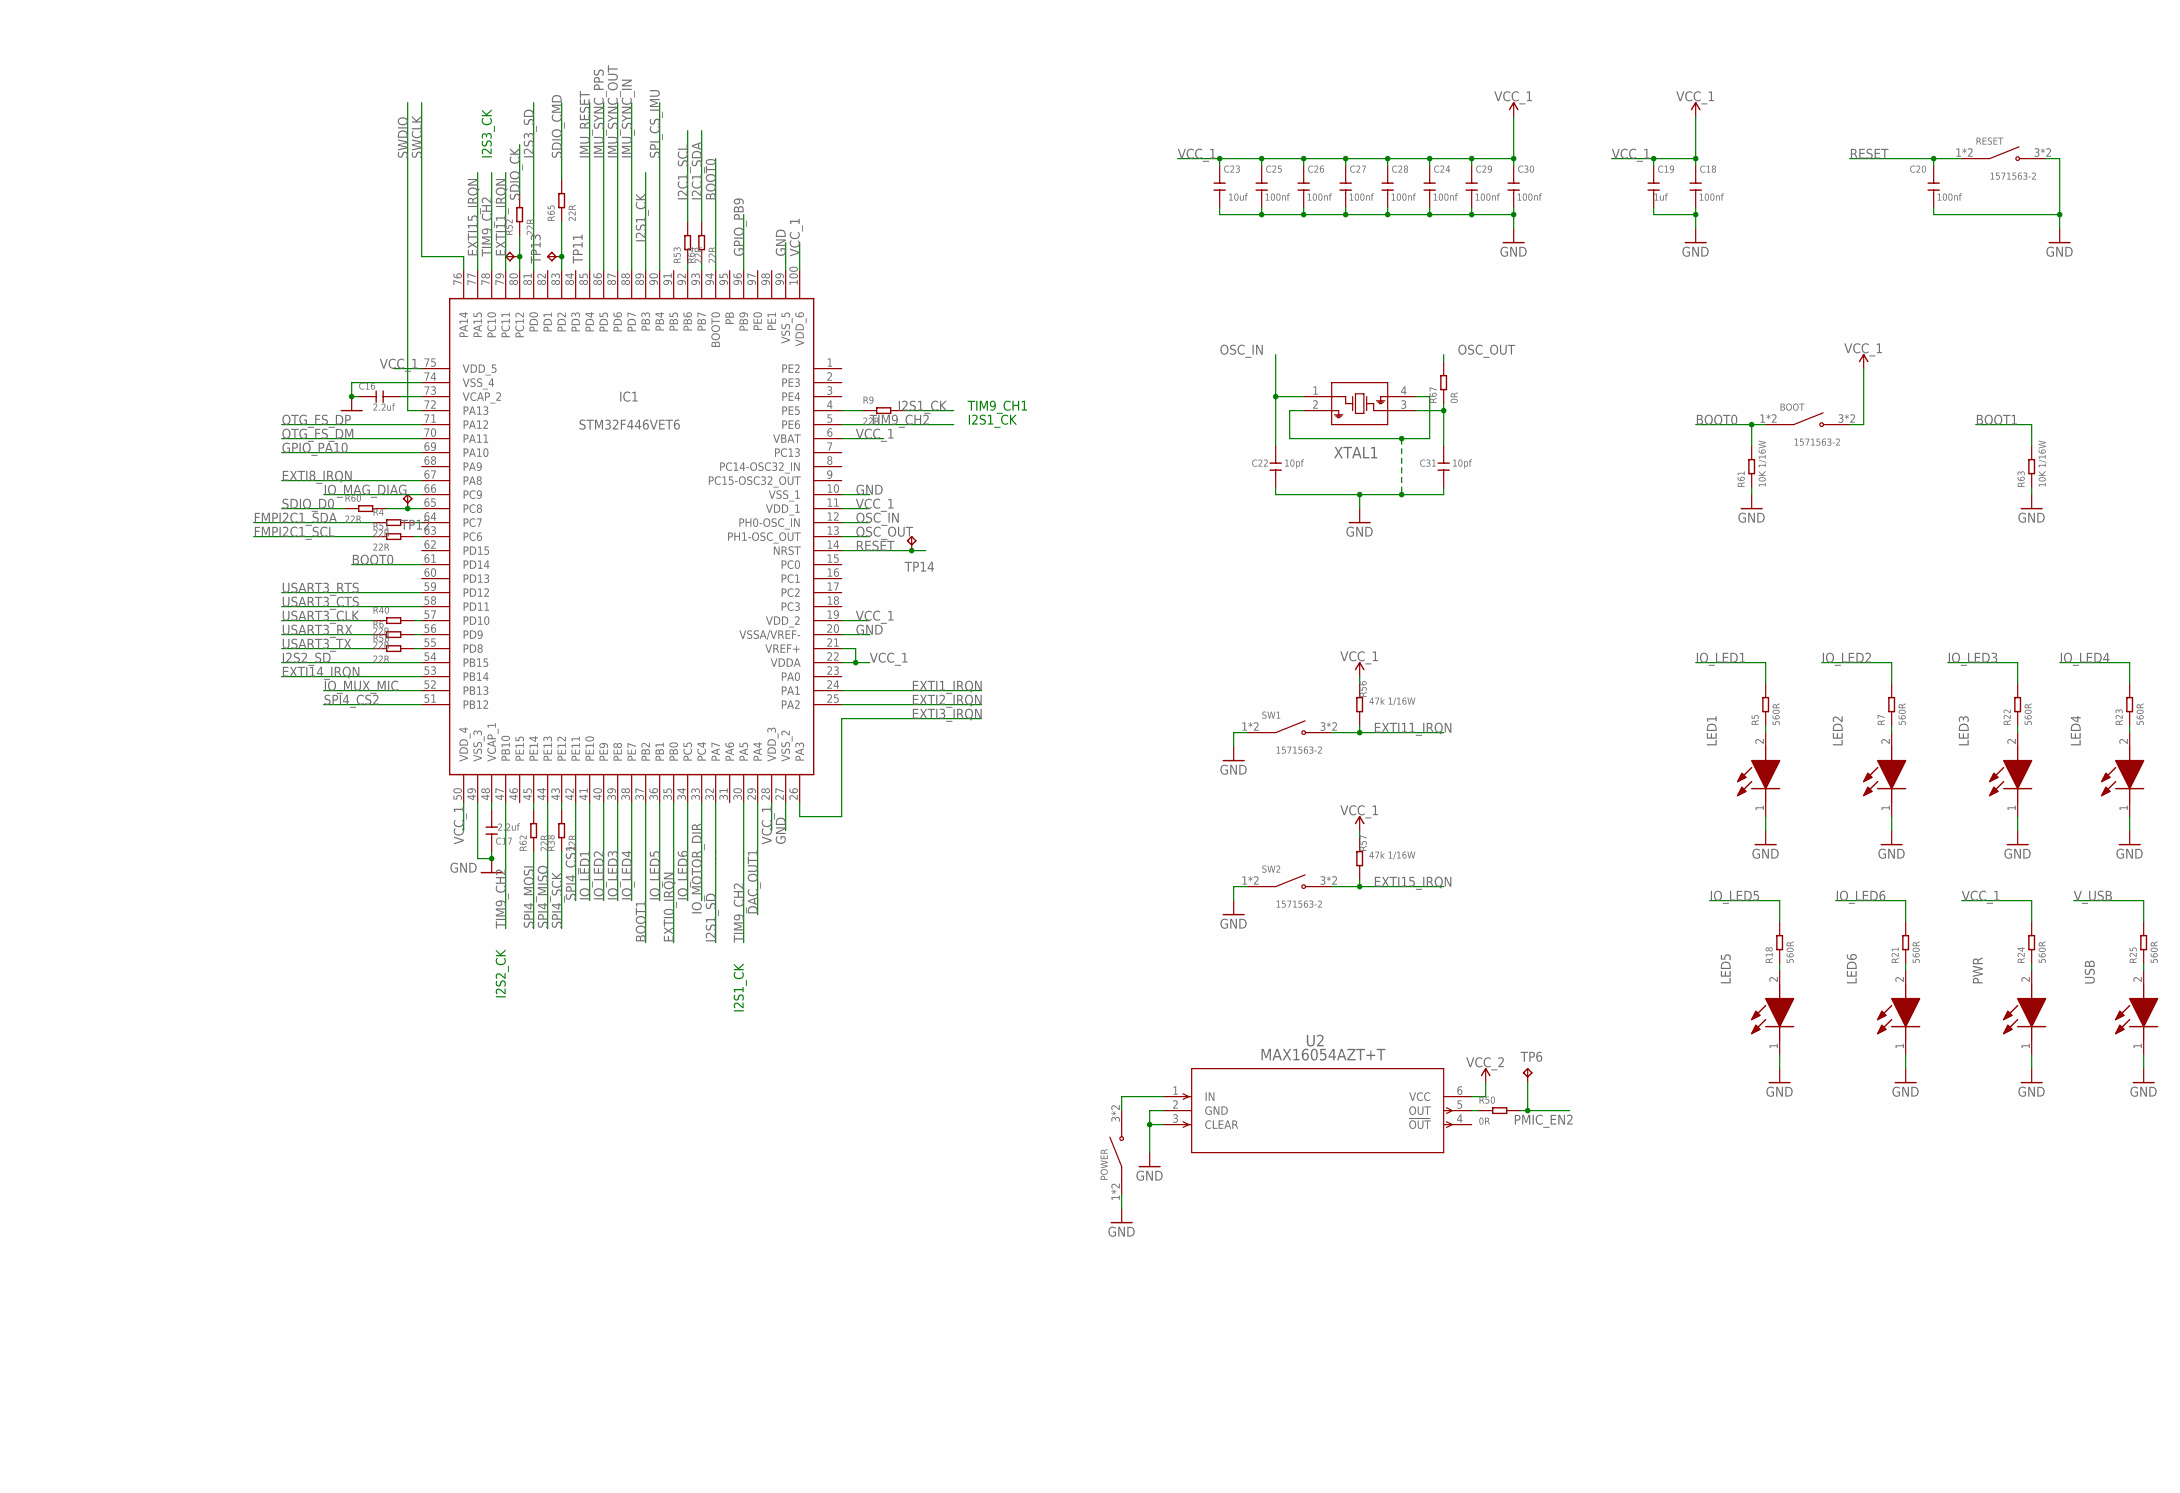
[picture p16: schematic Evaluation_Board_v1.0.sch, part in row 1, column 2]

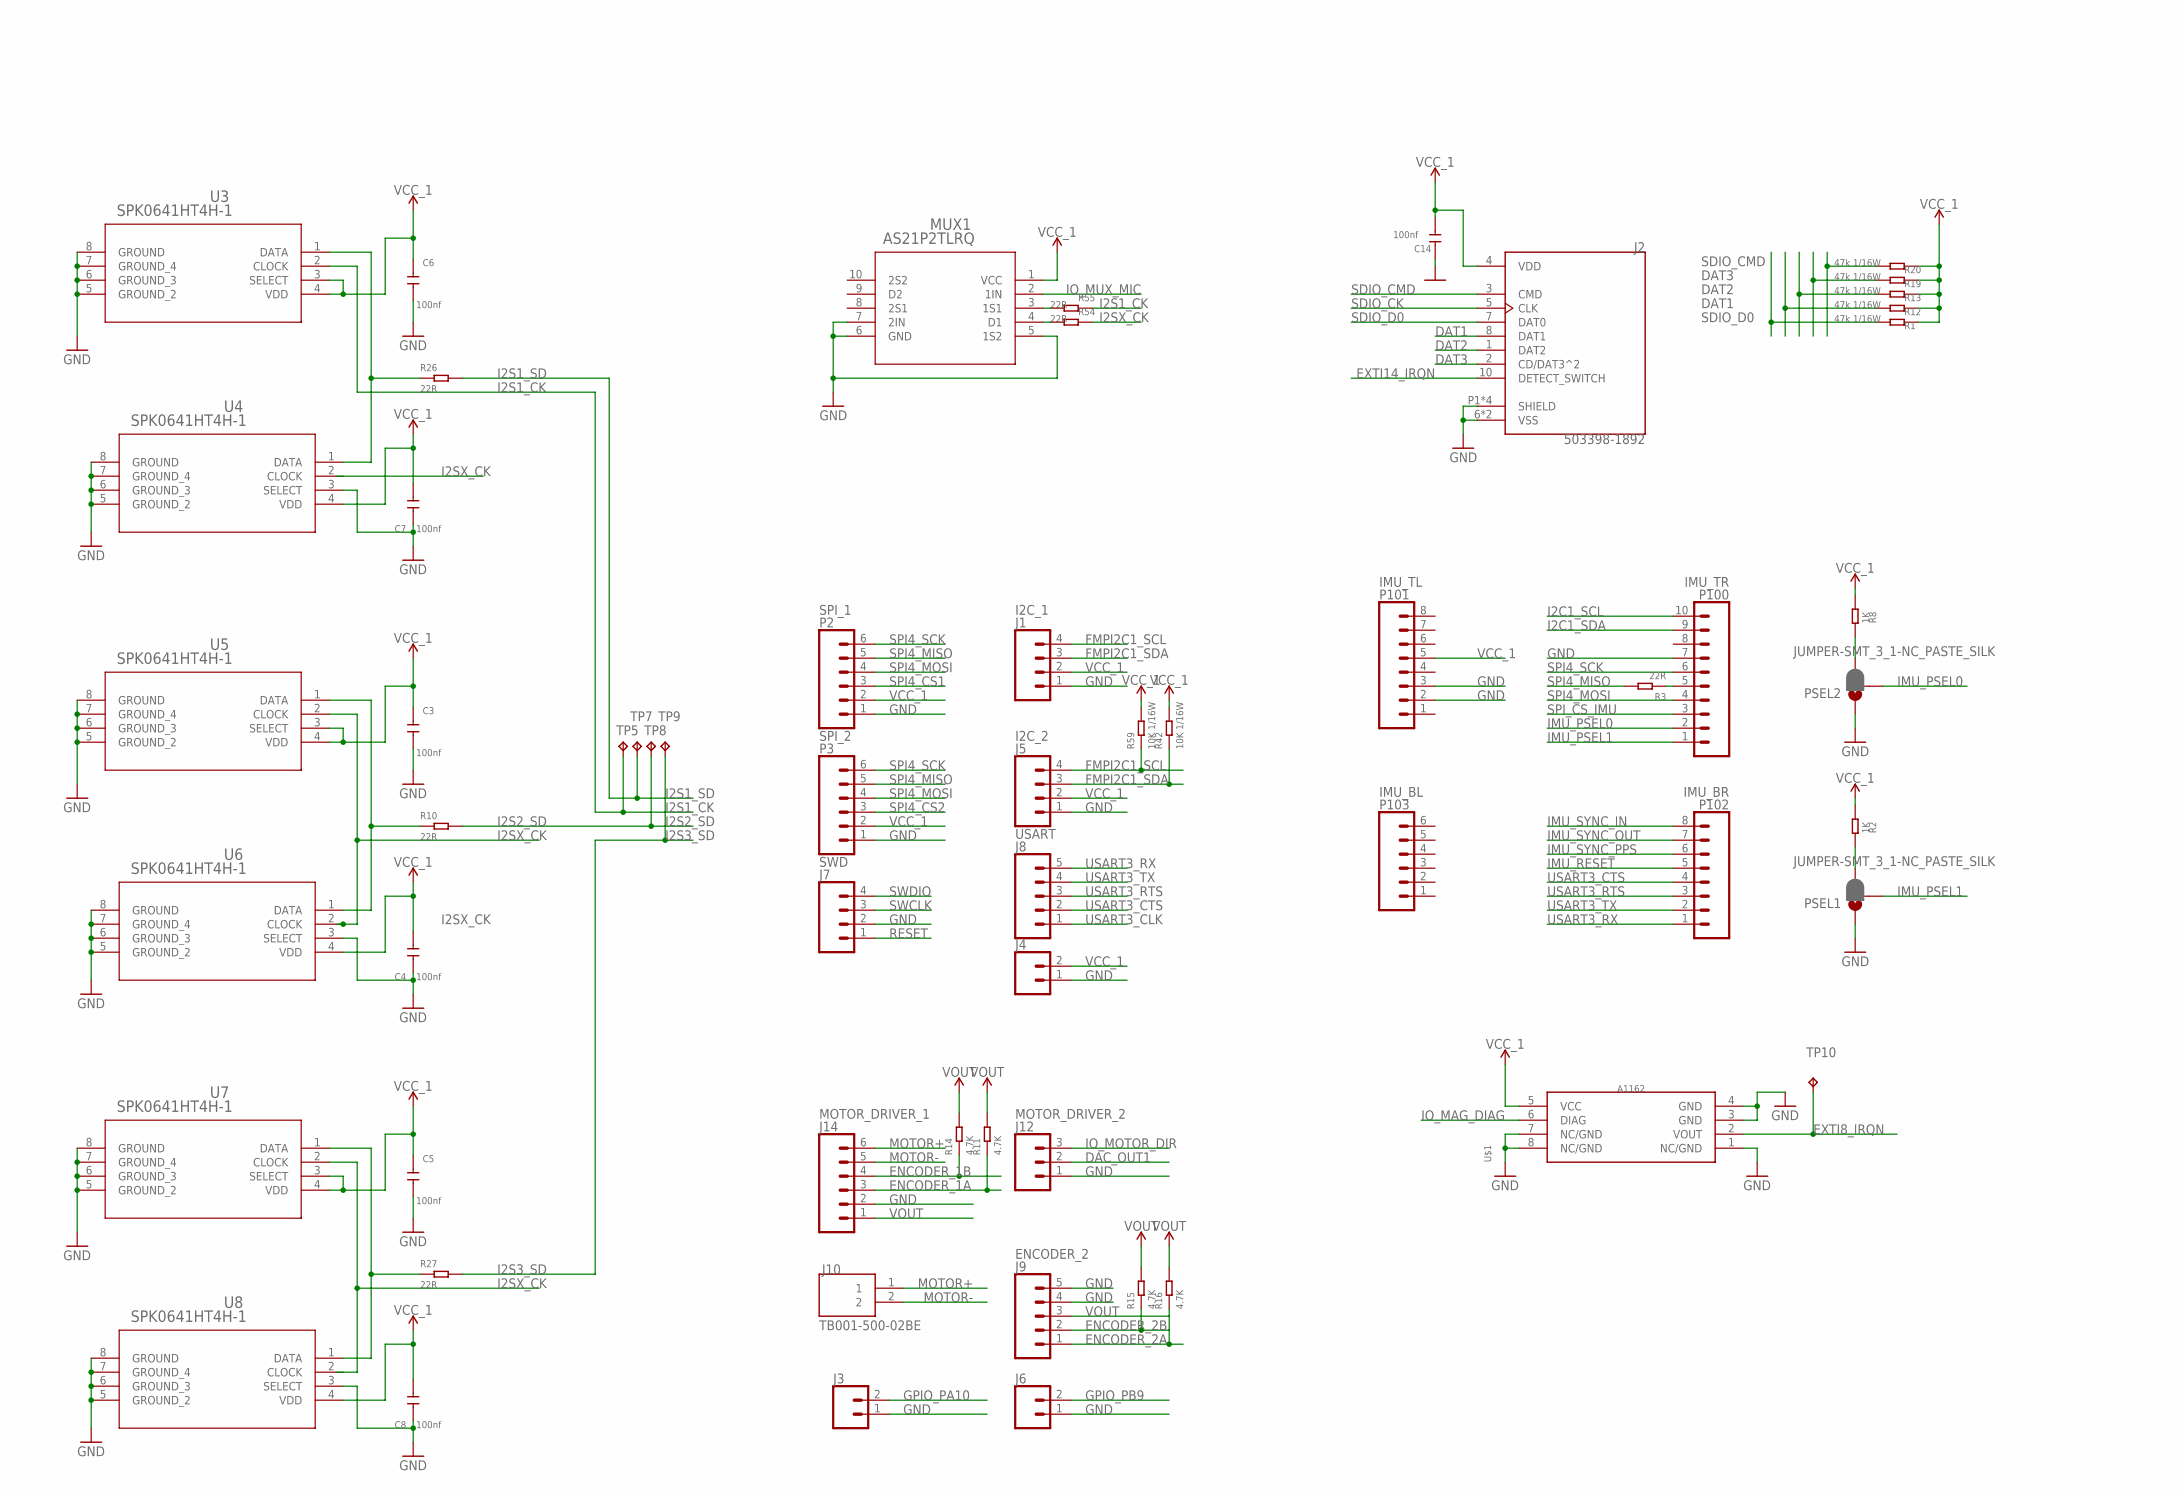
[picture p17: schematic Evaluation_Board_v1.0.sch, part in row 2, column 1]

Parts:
BOOT: 1571563-2; SW_1571563-2
C1, C3, C4, C5, C6, C7, C8, C14, C18, C20, C24, C25, C26, C27, C28, C29, C30, C33, C34: 100nf; C0402
C2, C19: 1uf; C0402
C15, C32: TPSA476K006R0800; CAPPM3216X180N
C16, C17: 2.2uf; C0603
C22, C31, C40: 10pf; C0402
C23, C36: 10uf; C0603
C38: 33pf; C0402
C39: 330pf; C0402
C41: 22uf; C0805
CHRG: SML-P12MTT86R; LEDM106X25N
CP1: USBLC6-2P6; USBLC62P6
CR1: L6920D; TSSOP8_STM
IC1: STM32F446VET6; QFP50P1600X1600X160-100N
J1: I2C_1; 1X04
J2: 503398-1892; MOLEX_503398-1892
J3, J4, J6: CONN_02; 1X02
J5: I2C_2; 1X04
J7: SWD; 1X04
J8: USART; 1X05
J9: ENCODER_2; 1X05
J10: TB001-500-02BE; CUI_TB001-500-02BE
J12: MOTOR_DRIVER_2; 1X03
J14: MOTOR_DRIVER_1; MOLEX-1X6
JP1, JP4: JUMPER-SMT_3_1-NC_PASTE_SILK; SMT-JUMPER_3_1-NC_PASTE_SILK
JST_BAT: S2B-PH-K-S(LF)(SN); JST_S2B-PH-K-S(LF)(SN)
L1: UP1B-100-R; INDM9060X500N
L3: CDRH3D16_HPNP-2R2NC; CDRH3D16HPNP2R2NC
LED1, LED2, LED3, LED4, LED5, LED6: SML-P12MTT86R; LEDM106X25N
MUX1: AS21P2TLRQ; QFN10_1P8X1P4X0P5_STM
P2: SPI_1; 1X06
P3: SPI_2; 1X06
P100: IMU_TR; 1X10
P101: IMU_TL; 1X08
P102: IMU_BR; 1X08
P103: IMU_BL; 1X06
POWER: 1571563-2; SW_1571563-2
PSEL1, PSEL2: JUMPER-SMT_3_1-NC_PASTE_SILK; SMT-JUMPER_3_1-NC_PASTE_SILK
PWR: SML-P12MTT86R; LEDM106X25N
Q1, Q2, Q3, Q4: BSS138; SOT95P240X111-3N
R1, R12, R13, R17, R19, R20, R41, R56, R57: 47k 1/16W; R0402
R2, R8, R36, R37: 1K; R0603
R3, R4, R6, R9, R10, R26, R27, R38, R40, R51, R52, R53, R54, R55, R58, R60, R62, R64, R65: 22R; R0402
R5, R7, R18, R21, R22, R23, R24, R25, R39: 560R; R0603
R11, R14, R15, R16: 4.7K; R0402
R28, R29, R30, R31, R32, R33, R34, R35, R42, R59, R61, R63: 10K 1/16W; R0402
R43: 324K; R0603
R44: 105K; R0603
R45: 121K; R0603
R46: 15K; R0603
R47, R48, R49, R50: 0R; R0805
R67: 0R; R0402
RESET: 1571563-2; SW_1571563-2
SW1, SW2: 1571563-2; SW_1571563-2
TP1, TP2, TP3, TP4, TP5, TP6, TP7, TP8, TP9, TP10, TP11, TP12, TP13, TP14: TPB1,27; B1,27
U1: LTC3558EUDPBF; QFN-20_UD_LIT
U2: MAX16054AZT+T; 21-0114C_MXM
U3, U4, U5, U6, U7, U8: SPK0641HT4H-1; SPK0641HT4H-1_KNO
U$1: A1162; A1162-8
UC1: 2013499-1
USB: SML-P12MTT86R; LEDM106X25N
XTAL1: NX2520SA-16MHZ; NX2520SA_NDK

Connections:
BAT: C36.2, R49.1, U1.2 (BAT), U1.7 (PVIN1), U1.8 (PVIN2)
BOOT0: BOOT.1 (COM), BOOT.2 (COM), IC1.61 (PD14), IC1.94 (BOOT0), R61.2
BOOT1: IC1.37 (PB2), R63.2
DAC_OUT1: IC1.29 (PA4), J12.2
DAT1: J2.8 (DAT1), R12.1
DAT2: J2.1 (DAT2), R13.1
DAT3: J2.2 (CD/DAT3^2), R19.1
ENCODER_1A: J14.3, Q1.3 (D), R11.1, R29.1
ENCODER_1B: J14.4, Q2.3 (D), R14.1, R31.1
ENCODER_2A: J9.1, Q3.3 (D), R16.1, R33.1
ENCODER_2B: J9.2, Q4.3 (D), R15.1, R35.1
EXTI0_IRQN: IC1.35 (PB0), Q2.2 (S), R30.1
EXTI1_IRQN: IC1.24 (PA1), Q3.2 (S), R32.1
EXTI2_IRQN: IC1.25 (PA2), Q4.2 (S), R34.1
EXTI3_IRQN: IC1.26 (PA3), Q1.2 (S), R28.1
EXTI8_IRQN: IC1.67 (PA8), TP10.TP, U$1.2 (VOUT)
EXTI11_IRQN: IC1.79 (PC11), R56.1, SW1.3 (NO), SW1.4 (NO)
EXTI14_IRQN: IC1.53 (PB14), J2.10 (DETECT_SWITCH)
EXTI15_IRQN: IC1.77 (PA15), R57.1, SW2.3 (NO), SW2.4 (NO)
FMPI2C1_SCL: J1.4, J5.4, R51.1, R59.1
FMPI2C1_SDA: J1.3, J5.3, R4.1, R42.1
GND: C1.1, C2.1, C3.1, C4.1, C5.1, C6.1, C7.1, C8.1, C14.2, C15.2 (-), C16.1, C17.1, C18.1, C19.1, C20.1, C22.1, C23.1, C24.1, C25.1, C26.1, C27.1, C28.1, C29.1, C30.1, C31.1, C32.2 (-), C33.2, C34.1, C36.1, C41.1, CP1.2 (GND), CR1.1 (FB), CR1.6 (GND), IC1.10 (VSS_1), IC1.20 (VSSA/VREF-), IC1.27 (VSS_2), IC1.49 (VSS_3), IC1.74 (VSS_4), IC1.99 (VSS_5), J1.1, J2.6 (VSS), J2.9 (VSS), J2.P1 (SHIELD), J2.P2 (SHIELD), J2.P3 (SHIELD), J2.P4 (SHIELD), J3.1, J4.1, J5.1, J6.1, J7.2, J9.4, J9.5, J12.1, J14.2, JP1.1, JP4.1, JST_BAT.1, LED1.1 (K), LED2.1 (K), LED3.1 (K), LED4.1 (K), LED5.1 (K), LED6.1 (K), MUX1.5 (1S2), MUX1.6 (GND), MUX1.7 (2IN), P2.1, P3.1, P100.7, P101.2, P101.3, POWER.1 (COM), POWER.2 (COM), PSEL1.1, PSEL2.1, PWR.1 (K), R17.1, R37.2, R41.1, R44.1, R61.1, R63.1, RESET.3 (NO), RESET.4 (NO), SW1.1 (COM), SW1.2 (COM), SW2.1 (COM), SW2.2 (COM), U1.1 (GND), U1.5 (EN1), U1.12 (SUSP), U1.17 (NTC), U1.21, U1.P$1 (21), U1.P$2 (21), U1.P$3 (21), U1.P$4 (21), U2.2 (GND), U2.3 (CLEAR), U3.5 (GROUND_2), U3.6 (GROUND_3), U3.7 (GROUND_4), U3.8 (GROUND), U4.3 (SELECT), U4.5 (GROUND_2), U4.6 (GROUND_3), U4.7 (GROUND_4), U4.8 (GROUND), U5.5 (GROUND_2), U5.6 (GROUND_3), U5.7 (GROUND_4), U5.8 (GROUND), U6.3 (SELECT), U6.5 (GROUND_2), U6.6 (GROUND_3), U6.7 (GROUND_4), U6.8 (GROUND), U7.5 (GROUND_2), U7.6 (GROUND_3), U7.7 (GROUND_4), U7.8 (GROUND), U8.3 (SELECT), U8.5 (GROUND_2), U8.6 (GROUND_3), U8.7 (GROUND_4), U8.8 (GROUND), U$1.1 (NC/GND), U$1.3 (GND), U$1.4 (GND), U$1.7 (NC/GND), U$1.8 (NC/GND), UC1.5, UC1.6 (5), UC1.7 (5), UC1.8 (5), UC1.9 (5), USB.1 (K), XTAL1.2, XTAL1.4
GPIO_PA10: IC1.69 (PA10), J3.2
GPIO_PB9: IC1.96 (PB9), J6.2
I2C1_SCL: P100.10, R53.2
I2C1_SDA: P100.9, R64.2
I2S1_CK: IC1.4 (PE5), IC1.89 (PB3), R9.1, R9.2, R55.2, TP5.TP, U3.2 (CLOCK)
I2S1_SD: IC1.32 (PA7), R26.2, TP7.TP
I2S2_SD: IC1.54 (PB15), R10.2, TP8.TP
I2S3_SD: IC1.81 (PD0), R27.2, TP9.TP
I2SX_CK: R54.2, U4.2 (CLOCK), U5.2 (CLOCK), U6.2 (CLOCK), U7.2 (CLOCK), U8.2 (CLOCK)
IMU_PSEL0: P100.2, PSEL2.2
IMU_PSEL1: P100.1, PSEL1.2
IMU_RESET: IC1.85 (PD4), P102.5
IMU_SYNC_IN: IC1.88 (PD7), P102.8
IMU_SYNC_OUT: IC1.87 (PD6), P102.7
IMU_SYNC_PPS: IC1.86 (PD5), P102.6
IO_LED1: IC1.41 (PE10), R5.2
IO_LED2: IC1.40 (PE9), R7.2
IO_LED3: IC1.39 (PE8), R22.2
IO_LED4: IC1.38 (PE7), R23.2
IO_LED5: IC1.36 (PB1), R18.2
IO_LED6: IC1.34 (PC5), R21.2
IO_MAG_DIAG: IC1.66 (PC9), U$1.6 (DIAG)
IO_MOTOR_DIR: IC1.33 (PC4), J12.3
IO_MUX_MIC: IC1.52 (PB13), MUX1.2 (1IN)
MODE: JP4.2, R17.2, U1.3 (MODE)
MOTOR+: J10.1, J14.6
MOTOR-: J10.2, J14.5
unnamed: C34.2, CR1.4 (REF)
unnamed: CR1.7 (LX), L1.2
unnamed: CP1.4 (D-OUT), UC1.2
unnamed: CP1.6 (D+OUT), UC1.3
unnamed: R36.1, U1.18 (PROG)
unnamed: R36.2, R37.1
unnamed: CHRG.2 (A), R39.1
unnamed: CR1.5 (!SHDN), JP1.2
unnamed: C38.2, R45.1
unnamed: C17.2, IC1.48 (VCAP_1)
unnamed: R50.1, U2.5 (OUT)
unnamed: C38.1, C40.2, R43.1, R44.2, R46.2, U1.13 (FB2)
unnamed: C39.2, R46.1
unnamed: C16.2, IC1.73 (VCAP_2)
unnamed: POWER.3 (NO), POWER.4 (NO), U2.1 (IN)
unnamed: PSEL1.3, R2.1
unnamed: MUX1.4 (D1), R54.1
unnamed: L3.1, U1.10 (SWCD2)
unnamed: C31.2, R67.1, XTAL1.3
unnamed: PSEL2.3, R8.1
unnamed: C39.1, C40.1, U1.14 (VC2)
unnamed: L3.2, U1.9 (SWAB2)
unnamed: LED1.2 (A), R5.1
unnamed: MUX1.3 (1S1), R55.1
unnamed: LED2.2 (A), R7.1
unnamed: IC1.63 (PC6), R51.2
unnamed: LED5.2 (A), R18.1
unnamed: IC1.57 (PD10), R40.2
unnamed: LED6.2 (A), R21.1
unnamed: IC1.43 (PE12), R38.2
unnamed: LED3.2 (A), R22.1
unnamed: R10.1, U5.1 (DATA), U6.1 (DATA)
unnamed: LED4.2 (A), R23.1
unnamed: IC1.80 (PC12), R52.1, TP13.TP
unnamed: PWR.2 (A), R24.1
unnamed: IC1.92 (PB6), R53.1
unnamed: R25.1, USB.2 (A)
unnamed: IC1.64 (PC7), R4.2
unnamed: IC1.56 (PD9), R6.2
unnamed: IC1.55 (PD8), R58.2
unnamed: P100.5, R3.1
unnamed: IC1.65 (PC8), R60.2, TP12.TP
unnamed: R27.1, U7.1 (DATA), U8.1 (DATA)
unnamed: IC1.45 (PE14), R62.2
unnamed: IC1.93 (PB7), R64.1
unnamed: IC1.83 (PD2), R65.1, TP11.TP
unnamed: R26.1, U3.1 (DATA), U4.1 (DATA)
OSC_IN: C22.2, IC1.12 (PH0-OSC_IN), XTAL1.1
OSC_OUT: IC1.13 (PH1-OSC_OUT), R67.2
OTG_FS_DM: CP1.3 (D-IN), IC1.70 (PA11)
OTG_FS_DP: CP1.1 (D+IN), IC1.71 (PA12)
OUT: C15.1 (+), C33.1, CR1.8 (OUT), R48.1
PMIC_CHRG: CHRG.1 (K), U1.19 (!CHRG)
PMIC_EN2: R41.2, R50.2, TP6.TP, U1.15 (EN2)
RESET: C20.2, IC1.14 (NRST), J7.1, RESET.1 (COM), RESET.2 (COM), TP14.TP
SDIO_CK: J2.5 (CLK), R52.2
SDIO_CMD: J2.3 (CMD), R20.1, R65.2
SDIO_D0: J2.7 (DAT0), R1.1, R60.1
SPI4_CS1: IC1.42 (PE11), P2.3
SPI4_CS2: IC1.51 (PB12), P3.3
SPI4_MISO: IC1.44 (PE13), P2.5, P3.5, R3.2
SPI4_MOSI: P2.4, P3.4, P100.4, R62.1
SPI4_SCK: P2.6, P3.6, P100.6, R38.1
SPI_CS_IMU: IC1.90 (PB4), P100.3
SWCLK: IC1.76 (PA14), J7.3
SWDIO: IC1.72 (PA13), J7.4
TIM9_CH2: IC1.5 (PE6), IC1.30 (PA5), IC1.47 (PB10), IC1.78 (PC10)
USART3_CLK: J8.1, R40.1
USART3_CTS: IC1.58 (PD11), J8.2, P102.4
USART3_RTS: IC1.59 (PD12), J8.3, P102.3
USART3_RX: J8.5, P102.1, R6.1
USART3_TX: J8.4, P102.2, R58.1
VCC_1: BOOT.3 (NO), BOOT.4 (NO), C3.2, C4.2, C5.2, C6.2, C7.2, C8.2, C14.1, C18.2, C19.2, C23.2, C24.2, C25.2, C26.2, C27.2, C28.2, C29.2, C30.2, C32.1 (+), IC1.6 (VBAT), IC1.11 (VDD_1), IC1.19 (VDD_2), IC1.21 (VREF+), IC1.22 (VDDA), IC1.28 (VDD_3), IC1.50 (VDD_4), IC1.75 (VDD_5), IC1.100 (VDD_6), J1.2, J2.4 (VDD), J4.2, J5.2, JP1.3, L1.1, MUX1.1 (VCC), P2.2, P3.2, P101.5, Q1.1 (G), Q2.1 (G), Q3.1 (G), Q4.1 (G), R1.2, R2.2, R8.2, R12.2, R13.2, R19.2, R20.2, R24.2, R28.2, R30.2, R32.2, R34.2, R42.2, R47.2, R56.2, R57.2, R59.2, TP2.TP, U3.3 (SELECT), U3.4 (VDD), U4.4 (VDD), U5.3 (SELECT), U5.4 (VDD), U6.4 (VDD), U7.3 (SELECT), U7.4 (VDD), U8.4 (VDD), U$1.5 (VCC)
VCC_2: JP4.3, JST_BAT.2, R49.2, TP3.TP, U2.6 (VCC)
VOUT: J9.3, J14.1, R11.2, R14.2, R15.2, R16.2, R29.2, R31.2, R33.2, R35.2, R48.2, TP4.TP
VOUT2: C41.2, R43.2, R45.2, R47.1, U1.11 (VOUT2)
V_USB: C1.2, C2.2, CP1.5 (VBUS), R25.2, R39.2, TP1.TP, U1.16 (HPWR), U1.20 (VCC), UC1.1

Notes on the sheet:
I2S1_CK
TIM9_CH1
I2S3_CK
I2S2_CK

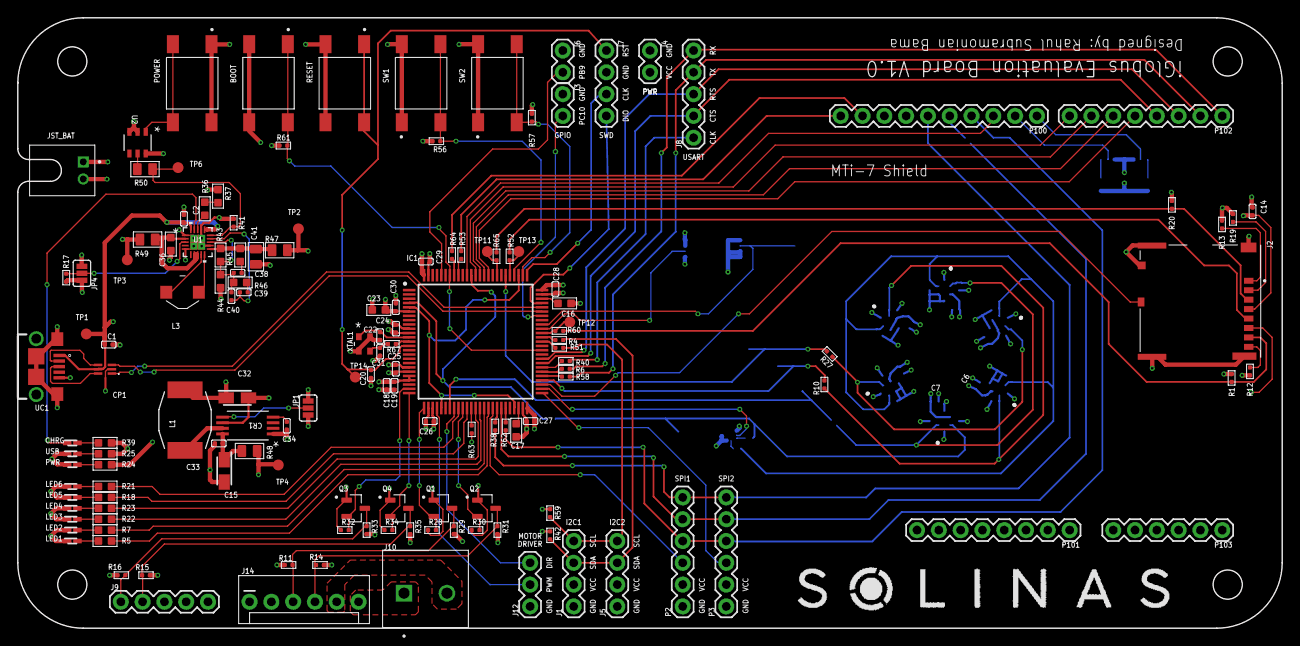
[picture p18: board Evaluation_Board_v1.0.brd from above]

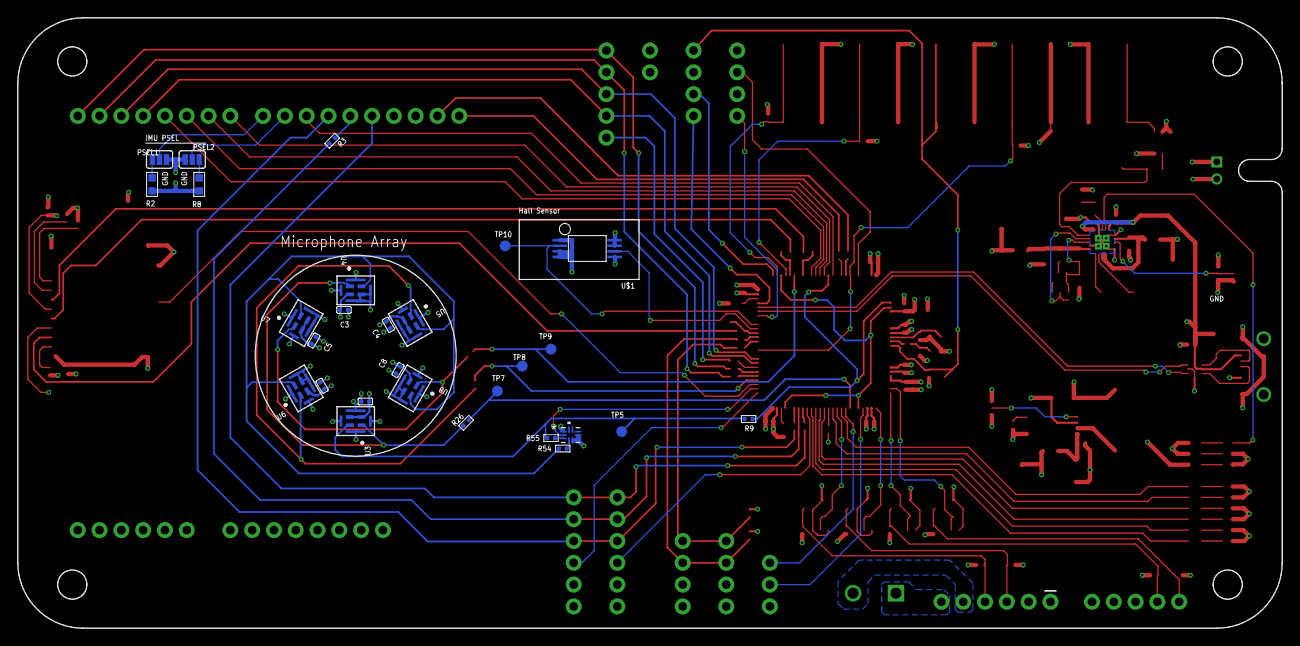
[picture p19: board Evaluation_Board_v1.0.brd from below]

Board: 4 copper layers, 147.3 x 71.1 mm, 172 parts (28 on the bottom side), 126 nets.

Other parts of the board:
U$2: SOLINAS-LOGO

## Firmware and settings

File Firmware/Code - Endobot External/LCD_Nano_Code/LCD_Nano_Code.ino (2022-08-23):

//Global Variables:
String T1, T2, T3, EN, Dir;
float prev_m = 0;

//********************************************************************LCD Display Global Requirements*****************************************************************************//
//Header Files:
#include <Adafruit_GFX.h>         // Core graphics library
#include <Adafruit_ILI9341.h>     // Hardware-specific library
#include <SdFat.h>                // SD Card & FAT filesystem library
#include <Adafruit_SPIFlash.h>    // SPI / QSPI flash library
#include <Adafruit_ImageReader.h> // Image-reading functions

//Interface Pins:
#define TFT_DC 9  //Data/Command line of Display
#define TFT_CS 10 //LCD Display chip select pin
#define TFT_RST 8 //LCD Display reset pin
#define SD_CS  4  //SD Card chip select pin
//Use default hardware SPI pins for MOSI, MISO and SCK - varies for different Arduino
//Arduino Mega SPI HW - MOSI (51), MISO (50) & SCK (52)
//Arduino Uno/Nano SPI HW - MOSI (11), MISO (12) & SCK (13)

#define USE_SD_CARD // Comment out this line to load from SPI/QSPI flash instead of SD card
#if defined(USE_SD_CARD)
  SdFat SD;  // SD card filesystem
  Adafruit_ImageReader reader(SD); // Image-reader object, pass in SD filesys
#else
  // SPI or QSPI flash filesystem (i.e. CIRCUITPY drive)
  #if defined(__SAMD51__) || defined(NRF52840_XXAA)
    Adafruit_FlashTransport_QSPI flashTransport(PIN_QSPI_SCK, PIN_QSPI_CS,
      PIN_QSPI_IO0, PIN_QSPI_IO1, PIN_QSPI_IO2, PIN_QSPI_IO3);
  #else
    #if (SPI_INTERFACES_COUNT == 1)
      Adafruit_FlashTransport_SPI flashTransport(SS, &SPI);
    #else
      Adafruit_FlashTransport_SPI flashTransport(SS1, &SPI1);
    #endif
  #endif
  Adafruit_SPIFlash    flash(&flashTransport);
  FatFileSystem        filesys;
  Adafruit_ImageReader reader(filesys); // Image-reader, pass in flash filesys
#endif

Adafruit_ILI9341 tft = Adafruit_ILI9341(TFT_CS, TFT_DC, TFT_RST);
ImageReturnCode stat;  // Status from image-reading functions (success or failure)

//****************************************************************************************************************************************************************************//

//Received Data Decoding Function:
void string_processor(String data)
{
  int index_1 = data.indexOf("a"); //stores the address of "a" in index_1
  int index_2 = data.indexOf("b");
  int index_3 = data.indexOf("c");
  int index_4 = data.indexOf("d");
  int index_5 = data.indexOf("e");
 
  T1 = (data.substring(0, index_1)); //reads the string data from 0 to index_1 & stores in T1 (motor 1 temp)      
  T2 = (data.substring(index_1+1, index_2));  
  T3 = (data.substring(index_2+1, index_3));
  EN = (data.substring(index_3+1, index_4));
  Dir = (data.substring(index_4+1, index_5));
}

void setup() 
{
  Serial.begin(9600); //To receive data from Mega & for serial monitor debug

  //Display:
  LCD_Display_ini(); //Display initialisation function
  tft.setRotation(2); //fxn to set display direction 
  Serial.print(F("Loading LCD_Boot_Image to screen..."));
  stat = reader.drawBMP("/LCD_Boot_Image.bmp", tft, 0, 0); //Load full-screen BMP file 'LCD_Boot_Image.bmp' at position (0,0) (top left)
  //Notice the 'reader' object performs this, with 'tft' as an argument.
  reader.printStatus(stat);  //Displays status of printed image (success or failure)
  delay(3000); //Show image for 3 seconds
}


void loop() 
{
  if(Serial.available() > 2)
  {
    String data = Serial.readStringUntil('\n');
    string_processor(data); //Fxn to process received string data
  }
  
  if (millis() > prev_m + 2000)
  {
    tft.fillScreen(ILI9341_BLACK); //fxn to fill screen with black color
    tft.setRotation(1); //fxn to set display direction
    tft.setTextColor(ILI9341_WHITE); //fxn to set text color
    tft.setTextSize(3); //fxn to set text size
    tft.setCursor(0, 1); //fxn to set cursor size
    
    if( T1.toFloat() > 70) //Motor 1 Temp Check & Display
    {
      tft.setTextColor(ILI9341_RED); 
      tft.print("Motor 1 Temp:");
      tft.print(T1);
      tft.println(" C");
      tft.setTextColor(ILI9341_WHITE);
    }
    else
    {
      tft.print("Motor 1 Temp:");
      tft.print(T1);
      tft.println(" C");
    } 
    
    if( T2.toFloat() > 70) //Motor 2 Temp Check & Display
    {
      tft.setTextColor(ILI9341_RED); 
      tft.print("Motor 2 Temp:");
      tft.print(T2);
      tft.println(" C");
      tft.setTextColor(ILI9341_WHITE);
    }
    else
    {
      tft.print("Motor 2 Temp:");
      tft.print(T2);
      tft.println(" C");
    }

    tft.print("Endobot Temp:"); //Endobot Chamber Temp
    tft.print(T3);
    tft.println(" C");
    
    tft.print("Distance: "); //Encoder Distance display
    tft.print(EN);
    tft.println(Dir);
    
    prev_m = millis();
  }


int LCD_Display_ini()
{
  tft.begin(); //Initialize screen

  //The Adafruit_ImageReader constructor call (above, before setup()) accepts an uninitialized SdFat or FatFileSystem object. 
  //This MUST BE INITIALIZED before using any of the image reader functions!
  //Below code is for initialising flash memory & SD card with error reporting
  
  Serial.print(F("Initializing filesystem..."));
  #if defined(USE_SD_CARD)
    //SD card is pretty straightforward, a single call..
    if(!SD.begin(SD_CS, SD_SCK_MHZ(25))) //ESP32 requires 25 MHz limit
    { 
      Serial.println(F("SD begin() failed"));
      for(;;); //Fatal error, do not continue
    }
  #else
    //SPI or QSPI flash requires two steps, one to access the bare flash memory itself, then the second to access the filesystem within..
    if(!flash.begin()) 
    {
      Serial.println(F("flash begin() failed"));
      for(;;);
    }
    if(!filesys.begin(&flash)) 
    {
      Serial.println(F("filesys begin() failed"));
      for(;;);
    }
  #endif
      Serial.println(F("OK!")); 
}

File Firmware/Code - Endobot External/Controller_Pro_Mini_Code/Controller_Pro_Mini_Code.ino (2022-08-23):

//Interface Pins:
#define FB A4 //Forward/Backward Joystick
#define LR A3 //Left/Right Joystick
#define LP A1 //Endobot LED Pot
#define ELED 11 //Endobot LED On/Off
#define FH 12 //Forward position hold
#define RH 5 //Reverse position hold
#define POTL 10 //Endobot LED pot's backlit LED


//Global Variables:
int xpot, ypot, LEDpot;
int LEDpos, FHold, RHold;


void setup() 
{
  Serial.begin (9600); //Serial Data Transfer (Pro Mini to Mega)
  pinMode(ELED, INPUT_PULLUP);
  pinMode(FH, INPUT_PULLUP);
  pinMode(RH, INPUT_PULLUP);
  pinMode(POTL, OUTPUT);
}


void loop() 
{
  int count1 = 0, count2 = 0, count3 = 0;
 
  xpot = analogRead(FB);
  //Serial.println(xpot);
  delay(100);
  count1=(xpot==0)?1:log10(xpot)+1; 
  
  ypot = analogRead(LR);
  //Serial.println(ypot);
  delay(100);
  count2=(ypot==0)?1:log10(ypot)+1; 

  LEDpot = analogRead(LP);
  //Serial.println(LEDpot);
  delay(100);
  count3=(LEDpot==0)?1:log10(LEDpot)+1; 

  LEDpos = digitalRead(ELED);
  FHold = digitalRead(FH);
  RHold = digitalRead(RH);

  int mapped = map(LEDpot, 0, 1023, 0, 255);
  if(LEDpos == 0)
  {
    analogWrite(POTL, mapped);
  }

  else if(LEDpos == 1)
  {
    digitalWrite(POTL, LOW);
  }
  
  Serial.print(count1);
  Serial.print(count2);
  Serial.print(count3);
  Serial.print(xpot);
  Serial.print(ypot);
  Serial.print(LEDpot);
  
  Serial.print(LEDpos);
  Serial.print(FHold);
  Serial.println(RHold);
  
  //delay(500);
}

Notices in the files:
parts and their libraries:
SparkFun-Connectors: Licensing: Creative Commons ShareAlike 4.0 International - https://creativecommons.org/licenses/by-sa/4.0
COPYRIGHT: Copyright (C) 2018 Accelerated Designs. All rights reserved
